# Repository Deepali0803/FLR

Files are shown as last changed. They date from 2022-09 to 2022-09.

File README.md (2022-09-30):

# FLR--Flight-Computer
There are numerous flight computers available in the market. My goal was to design a flight computer with components that have reasonably low pricing to reduce the overall production cost, available in breakout boards, and widely available.

This Flight Computer for Landing Model Rocket is capable of:
1. Calculating Orientation
2. Calculating Altitude
3. Controlling pyros for deploying parachute and landing legs
4. Controlling two servo motors
5. Logging flight data
6. Accessing flight data

=> For orientation sensing on the rocket, IMU - Inertial Measurement Unit MPU-6050 is used with a built-in gyroscope and an accelerometer sensor.

=> For altitude sensing, BMP280 Barometric Pressure Sensor is used which measures the atmospheric density of the air surrounding it and it gets lower as you get higher up into the atmosphere. By measuring the change in atmospheric density we determine how high the rocket is above the ground.

=> N-channel mosfets are used to control parachutes, landing-like deployments, and firing motors.

=> Main brain of the computer is the widely available Atmega328 processor.

=> To log and access the flight data, SPI - Serial Peripheral Interface flash chip is used along with MicroSD Card.

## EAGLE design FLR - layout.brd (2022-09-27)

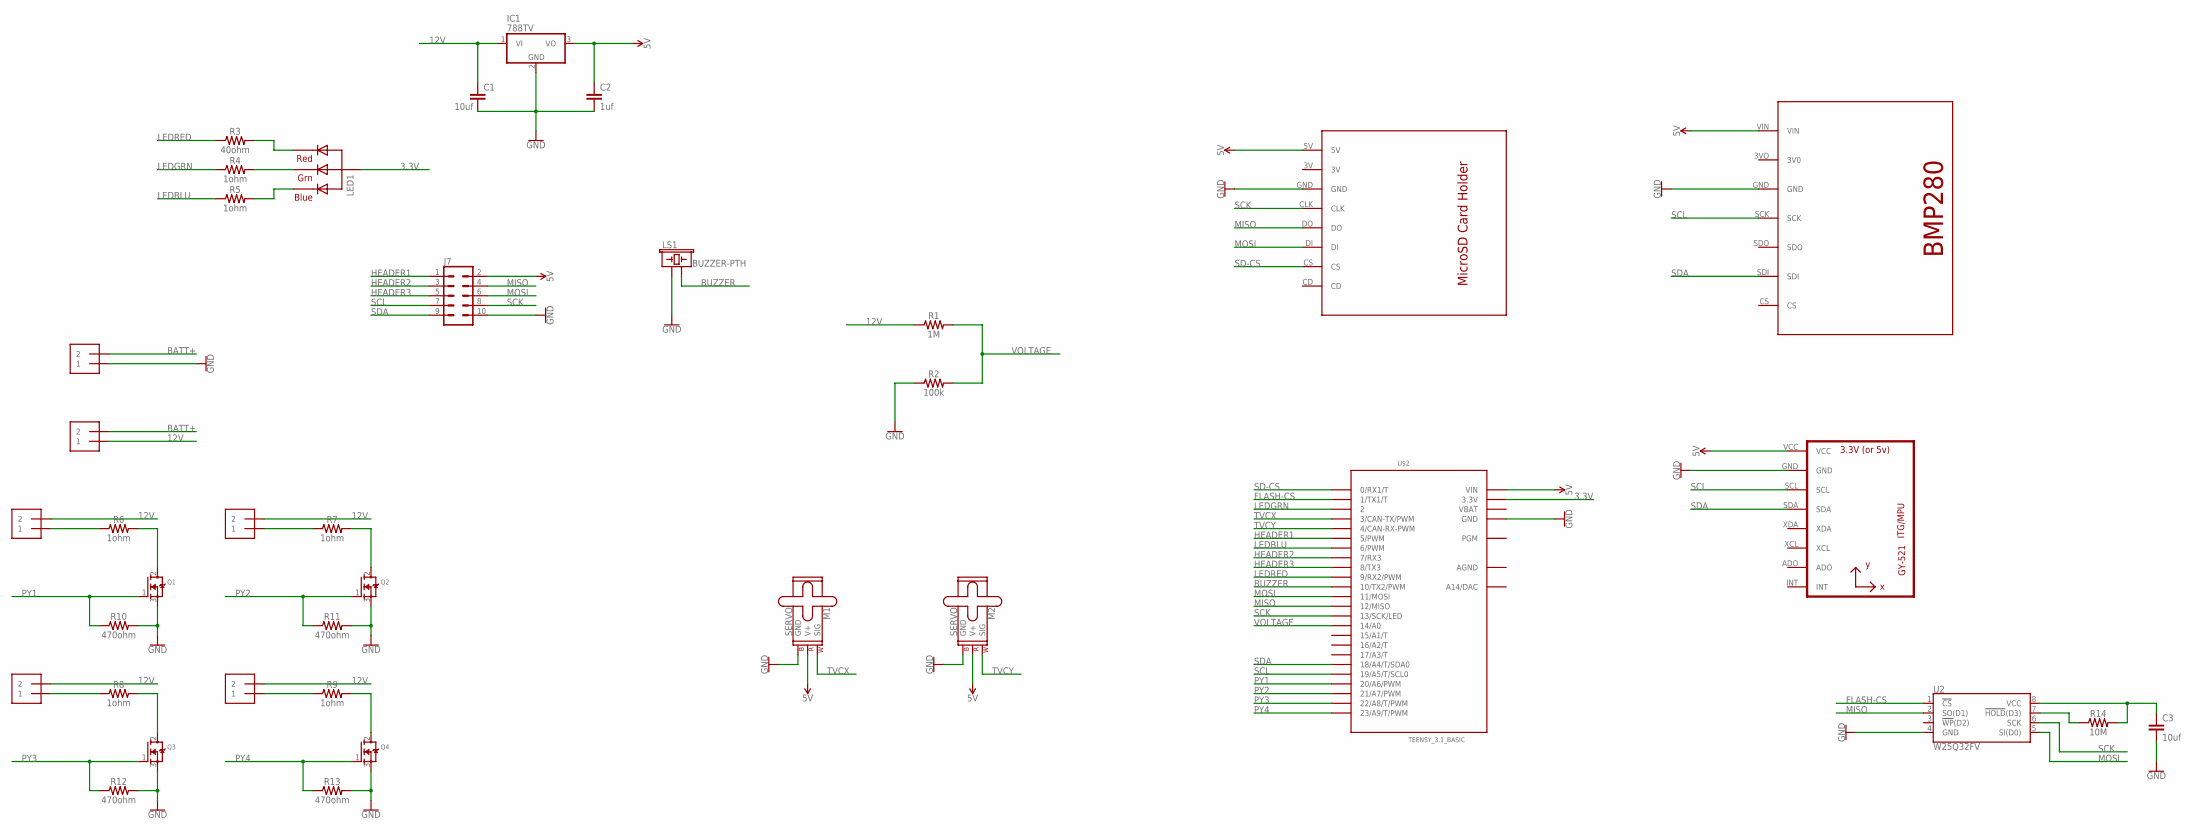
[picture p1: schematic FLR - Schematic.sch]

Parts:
C1, C3: 10uf; CAP-PTH-2.54
C2: 1uf; CAP-PTH-2.54
IC1: 788TV; TO220V
J1, J2, J3, J4, J5, J6: 1X2-3.5MM
J7: CONN_05X2NO_SILK; 2X5_NOSILK
LED1: RGBLED_CA-5MM; LED5MMRGB
LS1: BUZZER-PTH; BUZZER-12MM
M1, M2: SERVO; 1X03
Q1, Q2, Q3, Q4: MOSFET-NGDS_TO220V; TO220V
R1: 1M; AXIAL-0.3
R2: 100k; AXIAL-0.3
R3: 40ohm; AXIAL-0.3
R4, R5, R6, R7, R8, R9: 1ohm; AXIAL-0.3
R10, R11, R12, R13: 470ohm; AXIAL-0.3
R14: 10M; AXIAL-0.3
U1: GY-521MPU6050; GY-521
U2: W25Q32FV; SOIC-8
U$1: MICROSDCARD
U$2: TEENSY_3.1_BASIC
U$3: BMP280

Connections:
3.3V: LED1.2 (VCC), U$2.3.3V, U$2.3.3V1 (3.3V)
5V: C2.1, IC1.3 (VO), J7.2, M1.2 (V+), M2.2 (V+), U1.VCC, U$1.5V, U$2.VIN, U$3.VIN
12V: C1.1, IC1.1 (VI), J2.1, J3.2, J4.2, J5.2, J6.2, R1.P$1 (1)
AGND: U$2.AGND
BATT+: J1.2, J2.2
BUZZER: LS1.- (2), U$2.10 (10/TX2/PWM)
FLASH-CS: U2.1 (!CS!), U$2.1 (1/TX1/T)
GND: C1.2, C2.2, C3.2, IC1.2 (GND), J1.1, J7.10, LS1.+ (1), M1.3 (GND), M2.3 (GND), Q1.3 (S), Q2.3 (S), Q3.3 (S), Q4.3 (S), R2.P$1 (1), R10.P$2 (2), R11.P$2 (2), R12.P$2 (2), R13.P$2 (2), U1.GND, U2.4 (GND), U$1.GND, U$2.GND, U$2.GND1 (GND), U$3.GND
HEADER1: J7.1, U$2.5 (5/PWM)
HEADER2: J7.3, U$2.7 (7/RX3)
HEADER3: J7.5, U$2.8 (8/TX3)
LEDBLU: R5.P$1 (1), U$2.6 (6/PWM)
LEDGRN: R4.P$1 (1), U$2.2
LEDRED: R3.P$1 (1), U$2.9 (9/RX2/PWM)
MISO: J7.4, U2.2 (SO(D1)), U$1.DO, U$2.12 (12/MISO)
MOSI: J7.6, U2.5 (SI(D0)), U$1.DI, U$2.11 (11/MOSI)
unnamed: Q1.2 (D), R6.P$2 (2)
unnamed: LED1.1 (RED), R3.P$2 (2)
unnamed: LED1.3 (GREEN), R4.P$2 (2)
unnamed: LED1.4 (BLUE), R5.P$2 (2)
unnamed: J3.1, R6.P$1 (1)
unnamed: Q2.2 (D), R7.P$2 (2)
unnamed: J4.1, R7.P$1 (1)
unnamed: Q3.2 (D), R8.P$2 (2)
unnamed: J5.1, R8.P$1 (1)
unnamed: Q4.2 (D), R9.P$2 (2)
unnamed: J6.1, R9.P$1 (1)
unnamed: C3.1, R14.P$2 (2), U2.8 (VCC)
unnamed: R14.P$1 (1), U2.7 (!HOLD!(D3))
PY1: Q1.1 (G), R10.P$1 (1), U$2.20/A6 (20/A6/PWM)
PY2: Q2.1 (G), R11.P$1 (1), U$2.21/A7 (21/A7/PWM)
PY3: Q3.1 (G), R12.P$1 (1), U$2.22/A8 (22/A8/T/PWM)
PY4: Q4.1 (G), R13.P$1 (1), U$2.23/A9 (23/A9/T/PWM)
SCK: J7.8, U2.6 (SCK), U$1.CLK, U$2.13 (13/SCK/LED)
SCL: J7.7, U1.SCL, U$2.19/A5 (19/A5/T/SCL0), U$3.SCK
SD-CS: U$1.CS, U$2.0 (0/RX1/T)
SDA: J7.9, U1.SDA, U$2.18/A4 (18/A4/T/SDA0), U$3.SDI
TVCX: M1.1 (SIG), U$2.3 (3/CAN-TX/PWM)
TVCY: M2.1 (SIG), U$2.4 (4/CAN-RX-PWM)
VBAT: U$2.VBAT
VOLTAGE: R1.P$2 (2), R2.P$2 (2), U$2.14/A0

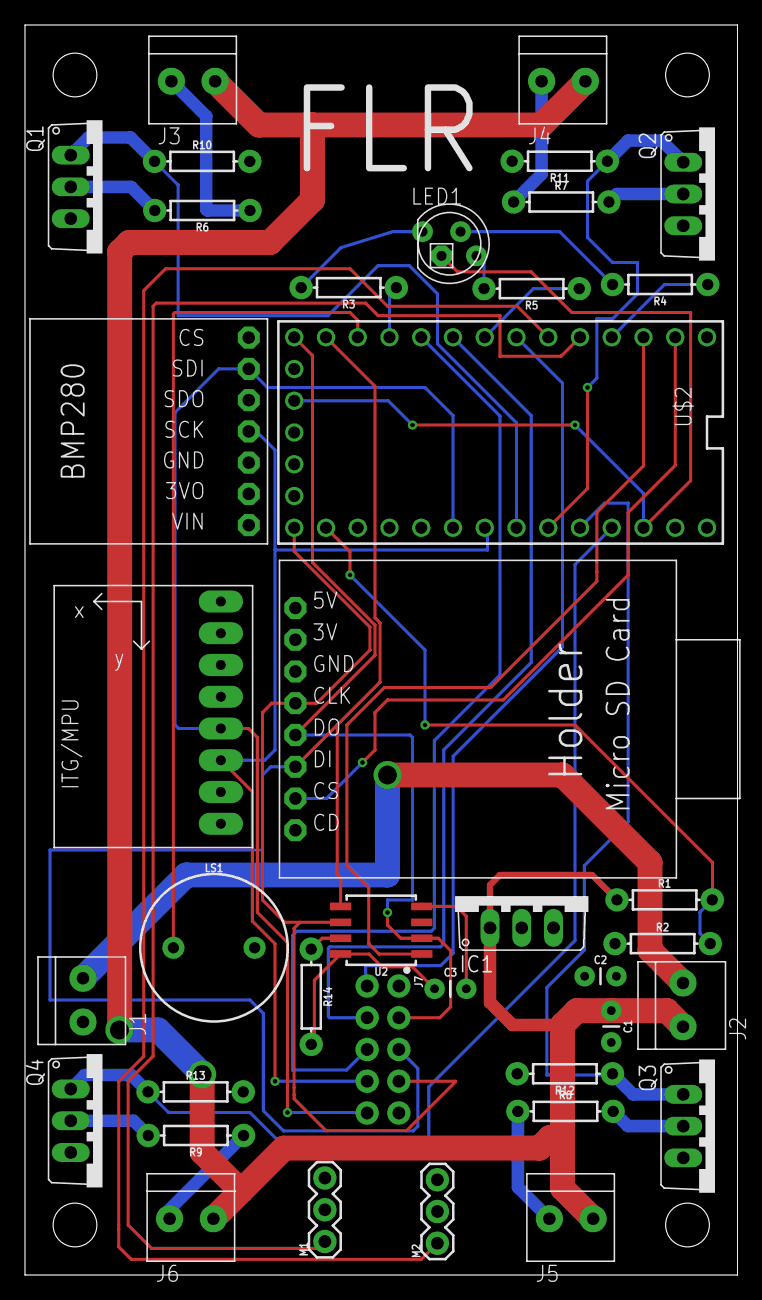
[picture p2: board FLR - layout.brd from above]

Board: 2 copper layers, 57.0 x 100.0 mm, 38 parts (0 on the bottom side), 39 nets.

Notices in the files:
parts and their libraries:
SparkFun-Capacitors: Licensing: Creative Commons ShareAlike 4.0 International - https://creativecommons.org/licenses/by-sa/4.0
